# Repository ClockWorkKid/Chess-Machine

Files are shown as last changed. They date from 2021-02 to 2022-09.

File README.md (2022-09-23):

# Chess-Machine
We implemented a chess playing robot that uses an XY plotter machine for manipulating the pieces, webcam for a view of the chessboard and the <a href="https://stockfishchess.org/download/">Stockfish</a> chess engine for calculating moves by the machine. This robot can play chess with a human player.

Demonstration video:
https://youtu.be/TBJXJzK3z6o

[](https://www.youtube.com/watch?v=TBJXJzK3z6o "Click on the image to watch video!")

## Contents
- [Materials Used](#materials-used)
- [Working Procedure](#working-procedure)
- [Hardware Setup](#hardware-setup)
- [Discussion](#discussion)
- [Team](#team)

## Materials Used
Here is a list of materials used for building the chess machine
- PVC board as the base material
- Art papers for coloring the board
- Nylon rods of 1cm diameter as the guide rails
- Linear bearings for sliding alond the rails
- Stepper motors and belts
- A 9g servo motor
- A tiny magnet for holding chess pieces
- IRF540 MOSFETs for stepper motor driver
- A cheap computer PSU
- Arduino UNO for controlling stepper motors
- Lots of wires
- Webcam
- Computer

## Working Procedure
The chess machine has an image based input, a chess engine that works in tandem with MATLAB as the processing unit, and the physical XY plotter that acts as the ouput.

### Detection of Board and Chess Pieces

When a game session starts, the interface prompts the user with a view from the webcam for cropping out the board region. This could be done automatically, but we kept it manual for better precision. The user can crop out the bounding box of the actual board region from the snapshot - this bounding box helps greatly in the detection of chess pieces. The bounding box can be converted to a 8x8 grid that represents the chess board as a table.

We made the board red and blue, and the chess pieces are black and white - this made the overall detection process much easier. The board can be detected using red and blue channels of the RGB image. The white and black chess pieces can be detected using the brightness level. Problem arises when there is overbright or shadowed regions in the chess board that messes with the detection of black and white pieces. For solving this, we trained a regression model for multi-class classification of colors in the board. First, using the "calibrate_samples3.m" funciton multiple samples of red, blue, white and black regions are sampled and then converted to a very small dataset. Then "myOneVsAll.m" funciton is used to trained the logistic regression network for a multi-class classification of color pixels on the chess board. After each pixel is identified as a separate color, we convert the natural board color into a more uniform color distribution where the chess pieces can be more accurately identified. 

In the "get_board3.m" function, an image sample taken by the webcam is first passed through the logistic regression network and then the color channels are used to seperate red, blue, white and black layers.

```
pixels = [ones(size(R)) , R , G , B] ; % unrolled rgb matrix
colors = 1./(1+exp(-(pixels*all_theta'))) > logistic_thres ; % logistic regression prediction
```

White pieces are shown as regions of higher brightness, and black pieces are shown as regions of lower brightness. These are represented as two separate masks, and after morphological opening of these masks and detecting regions, the location of each chess piece can be seen by the computer. 
```
WHITE = imopen(WHITE,strel('disk',noise));
WHITE = ~imopen(~WHITE,strel('disk',noise));
BLACK = imopen(BLACK,strel('disk',noise));
BLACK = ~imopen(~BLACK,strel('disk',noise));

whitePieces = imresize(imcrop(WHITE,stats.BoundingBox),[640 640]);
blackPieces = imresize(imcrop(BLACK,stats.BoundingBox),[640 640]);

%% Identifying objects

detect_white = regionprops(whitePieces,'BoundingBox','Centroid','Area');
detect_black = regionprops(blackPieces,'BoundingBox','Centroid','Area');

```

<figure align="center">
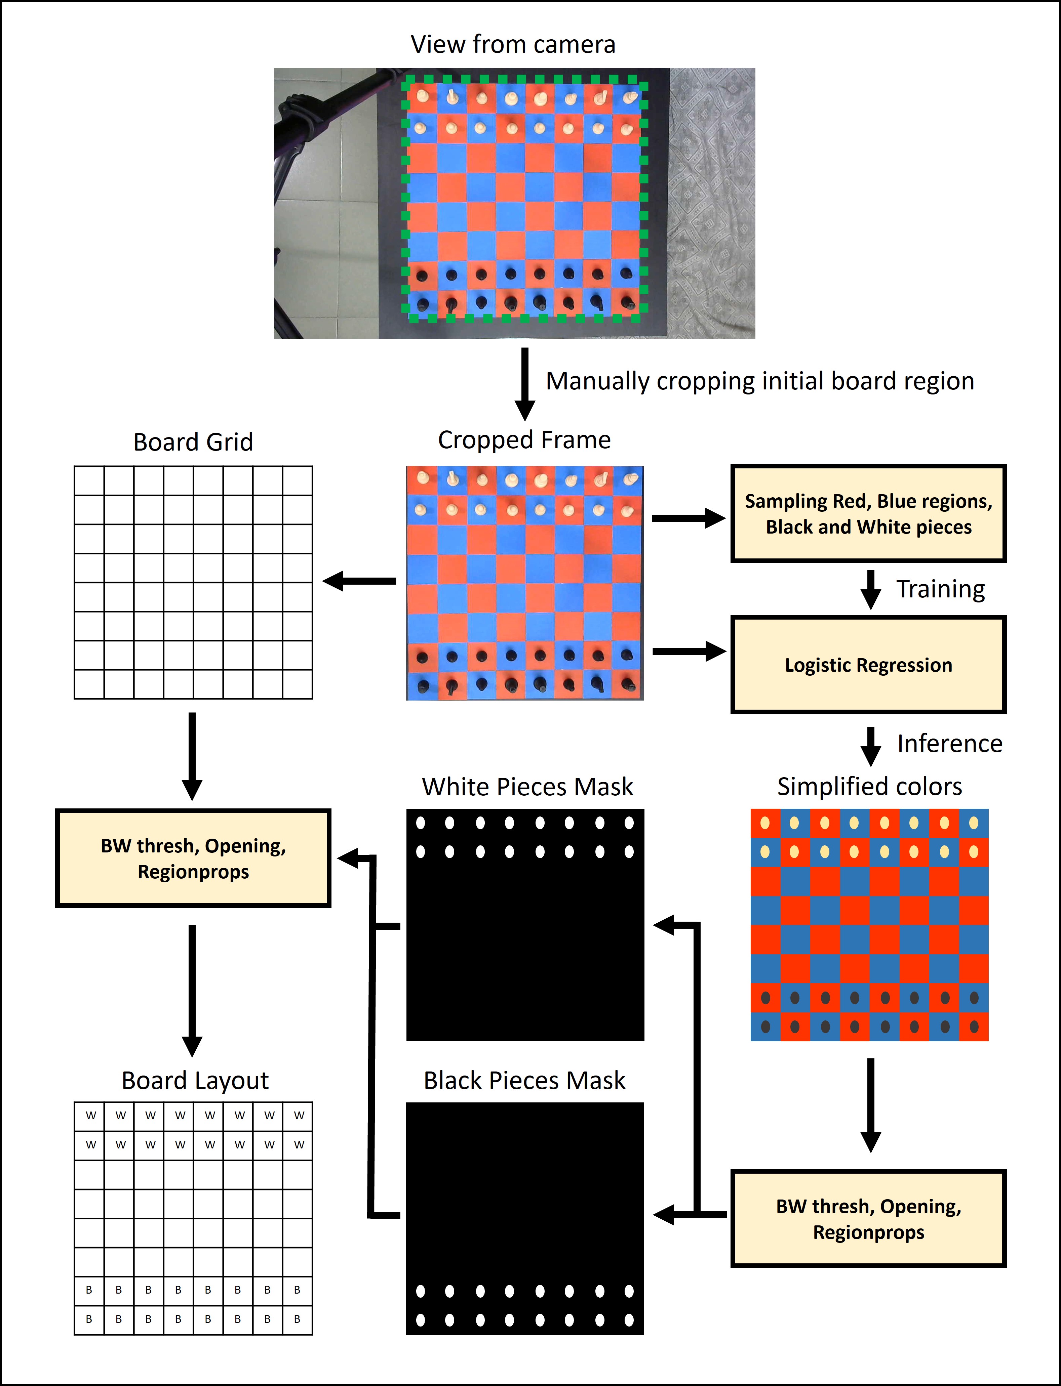
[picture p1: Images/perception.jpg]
    
    <figcaption>Perception framework</figcaption>
</figure>

The region detection function returns the centroids of each of the chess pieces, and we already know the bounding box of the entire board. The board bounding box is converted to a grid of 8x8 and the chess pieces are placed within that grid to know the board positions that are occupied by pieces in a tabular form. Using knowledge of the previous board configuration and comparing it with the current board configuration, we can understand which piece was recently moved. This information is then passed to the custom chess manager that retains memory of the board and checks for validity of moves. 

### Interpreting Board Configuration and Generating Moves

A generic chess game starts from a single position. The perception framework can identify the pieces on the board as black and white pieces only. We detect each piece by observing the displacement between two consecutive snapshots. This helps in determining piece movement, captures etc. The move is then passed to our own implementation of chess logic, that exports the current board configuration into a text format readable by the Stockfish chess engine. 

<figure align="center">
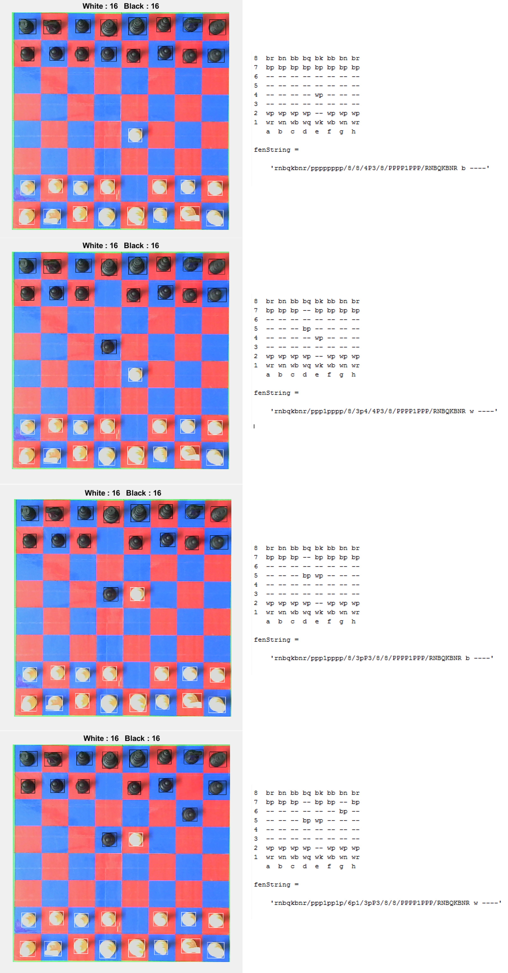
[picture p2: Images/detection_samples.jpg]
    
    <figcaption>Detecting moves and passing to stockfish</figcaption>
</figure>

```
board_new = get_board3(snapshot(cam));
difference_array = xor(board_prev,board_new);

%% implementation of chess logic to detect legality of move
y = checkLegal(b_board, difference_array);

%% update the current board configuration
update(b_board, difference_array)

%% convert to stockfish readable format
fenString = convert_to_fen(b_board)
pass_to_stockfish(fenString)
```

Stockfish can produce the next best move when any board configuration is passed as an input. We then apply a very simple path planning algorithm and send commands to the stepper motors via arduino to move around chess pieces as required by the move.

### Moving the Pieces Around

Say, we want to move a piece from (x1, y1) to (x2, y2). Pieces normally rest at the center of each block. Since the chess machine drags objects magnetically from below the board, direct line movement from block to block would result in conflict between pieces. To solve this, we drag the pieces along the cell borders. When a piece is to be moved, the XY plotter first grabs the piece from the center of a cell, drags it to the corner of the cell, and moves it along the cell edges as shown in the picture. After reaching the destination cell, it places it in the center of the 
target cell. When a piece is to be captured by the machine, the robot would first grab the captured piece, take it outside the chess board, and then replace the target position with the capturing piece. 

<figure align="center">
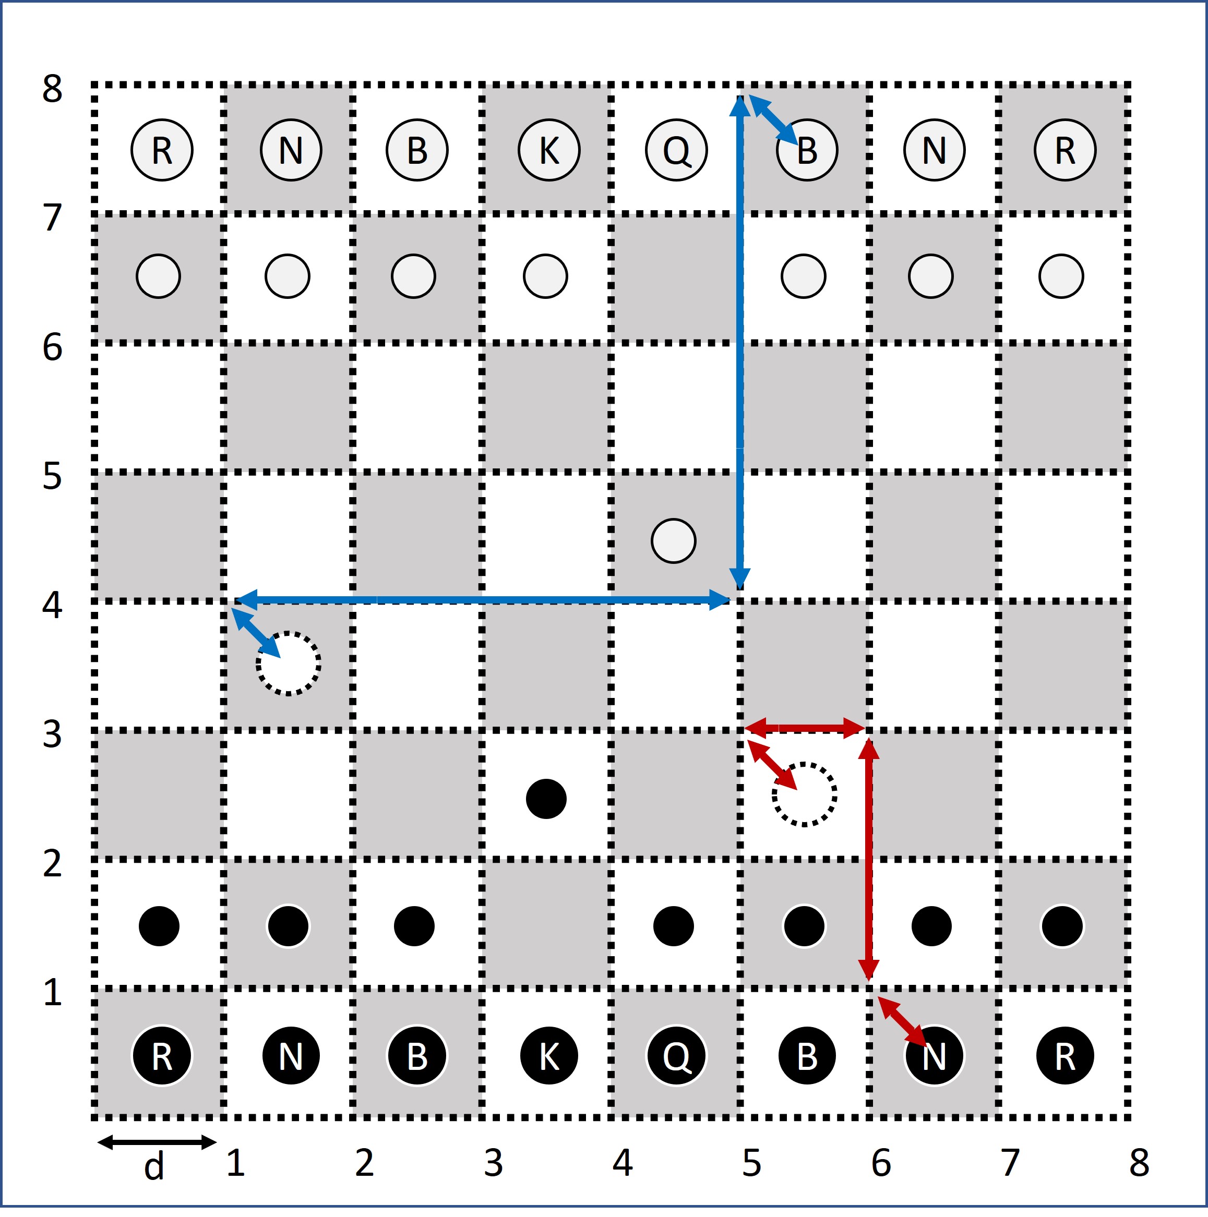
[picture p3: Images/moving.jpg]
    
    <figcaption>Moving around pieces</figcaption>
</figure>

## Hardware Setup

We made initial planning of the hardware using SolidWorks, keeping in mind the use of PVC as the base material for our setup. Some of the dimensions were later changed during implementation. These designs are available in the CAD folder.

<figure align="center">
    
    <figcaption>SolidWorks Design.</figcaption>
</figure>

The axes move on the nylon rails with the help of linear bearings. As pulleys for the stepper motor belts, we had used regular ball bearings. A servo was placed on the second axis, and it had a magnet attached to the tip. A video demonstration of the internals of the XY plotter after the motors were powered: https://youtube.com/shorts/JwAQECdfFwo

[](https://www.youtube.com/watch?v=JwAQECdfFwo "Click on the image to watch video!")

The hardware side of things is connected to Arduino (Arduino Stepper Code > xyplotter3). MATLAB communicates with Arduino via the Serial port and sends commands to it for moving the motors. Arduino moves the axes by switching the poles of the stepper motors. We manually calculated the number of steps required for the requried XY motion. As for the motor driver, we could have used dedicated ICs, but building the motor driver using MOSFETs was quite rewarding. The final circuit is placed inside a little white box to keep things neat. The motors were powered using a cheap computer PSU.

<figure align="center">
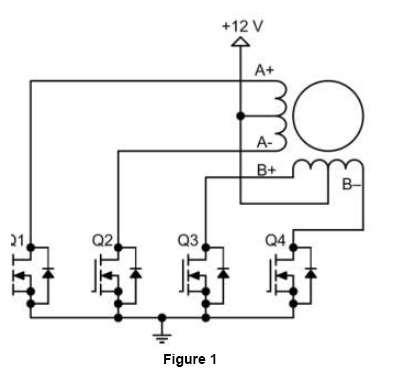
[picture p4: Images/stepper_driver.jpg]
    
    <figcaption>Motor Driver Schematics.</figcaption>
</figure>

## Gallery

<figure align="center">
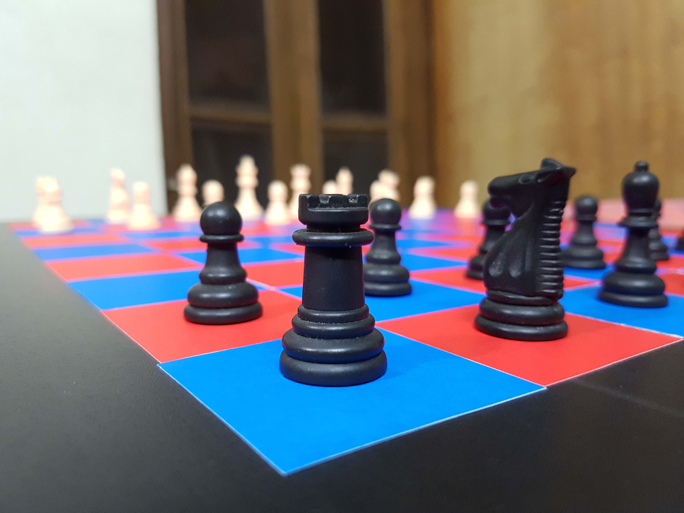
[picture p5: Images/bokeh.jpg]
    
    <figcaption>Starting the build</figcaption>
</figure>

<figure align="center">
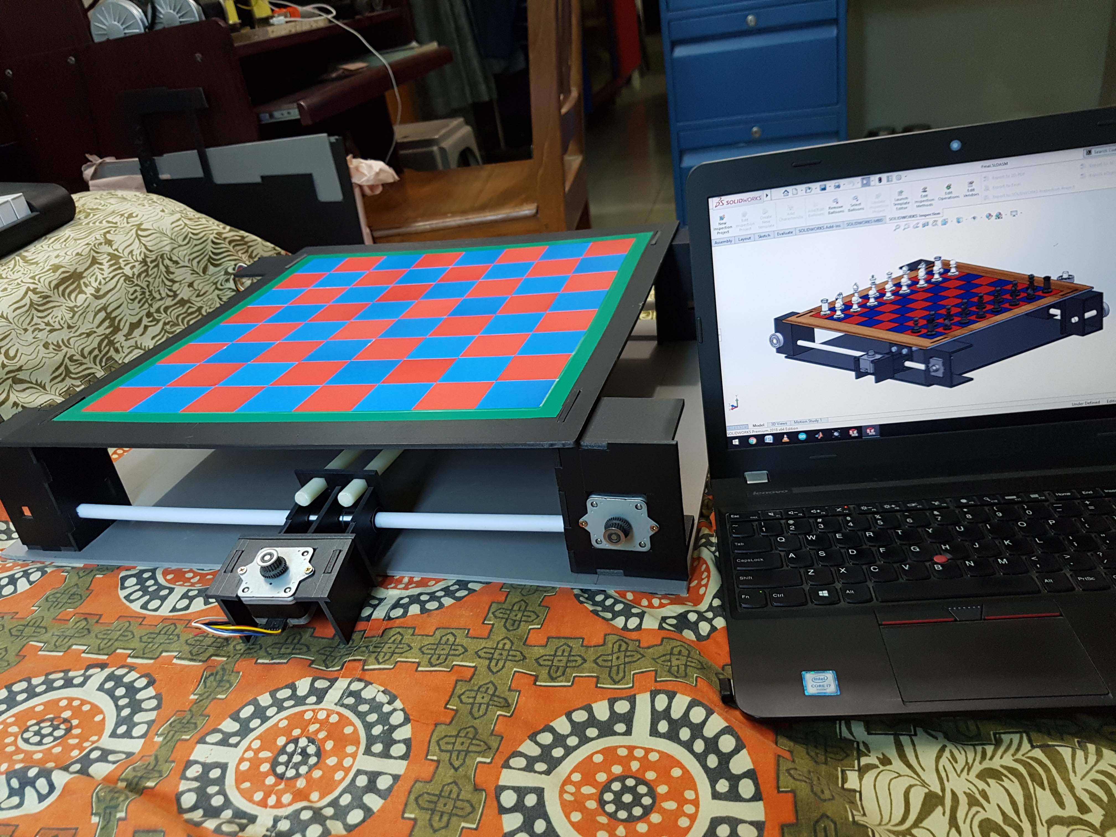
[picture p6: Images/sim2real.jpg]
    
    <figcaption>Bringing to reality</figcaption>
</figure>

<figure align="center">
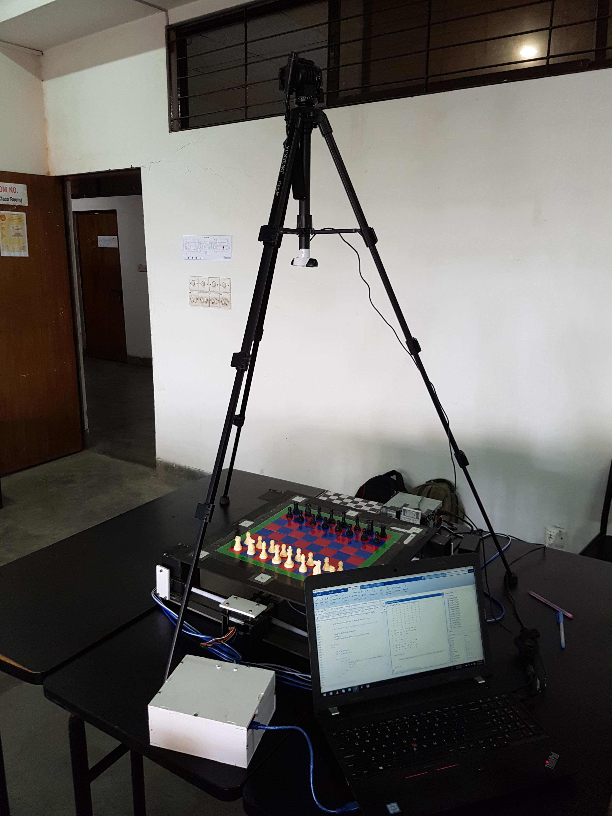
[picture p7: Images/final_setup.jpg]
    
    <figcaption>Setup for project demonstration</figcaption>
</figure>

## Discussion

There are a few shortcomings of the project:
- We have used very cheap materials for the physical hardware. The stepper motors and the belts were especially bad. The board was also malleable, and tended to bend around the center region. The guide-rails were nylon rods, also bendy. No complaints about electrical hardware, just the mechanical part could have been way much better. We stuck to cheap materials because they could be easily modified by hand without needing heavy machinery.
- For the image processing part, we made the board red-blue to easily identify the chess pieces on the board. Normally chess boards are black and white. At that time we didn't have much idea about machine learning or deep learning techniques. Chess pieces on a black and white board can be easily detected using object detection algorithms. Pieces also can be individually identified. Machine learning would also allow the processing to be more robust and environment independent.
- Could have used a dedicated servo motor driver.
- Could have implemented the system using a Raspberry Pi instead of a clunky laptop.

Things that would be cool to implement:
- Training an AI using reinforcement learning to play chess with people
- Remotely playing chess with other human players using the chess machine. (without needing to stare at a computer screen!)

## Team

- Mir Sayeed Mohammad (EEE) (github - https://github.com/ClockWorkKid)
- Shafin Bin Hamid (EEE) (github - https://github.com/shafinbinhamid)
- Himaddri Roy (EEE) (github - https://github.com/himu587)
- Md. Asif Iqbal (EEE)

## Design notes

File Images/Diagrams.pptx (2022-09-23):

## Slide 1

View from camera

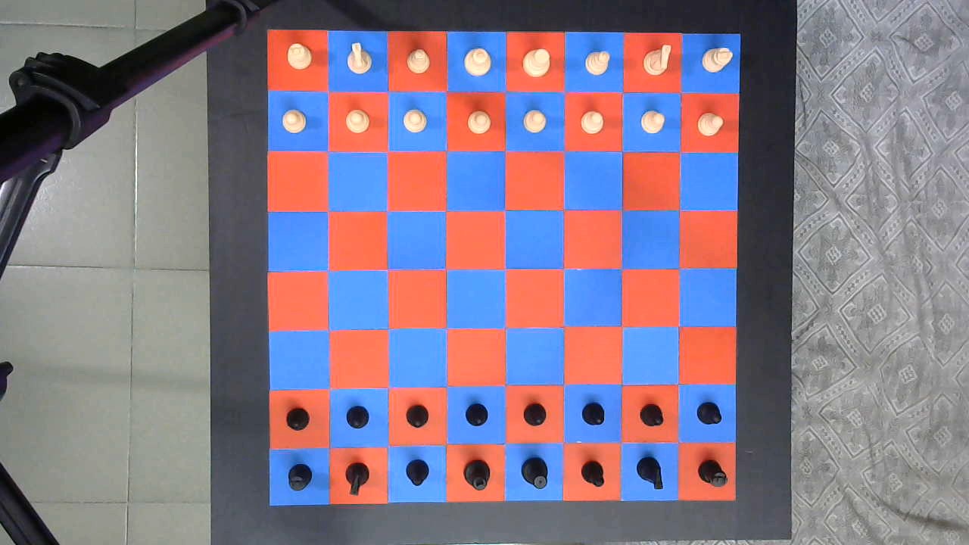
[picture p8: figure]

Manually cropping initial board region

Sampling Red, Blue regions, Black and White pieces

Board Grid

Cropped Frame

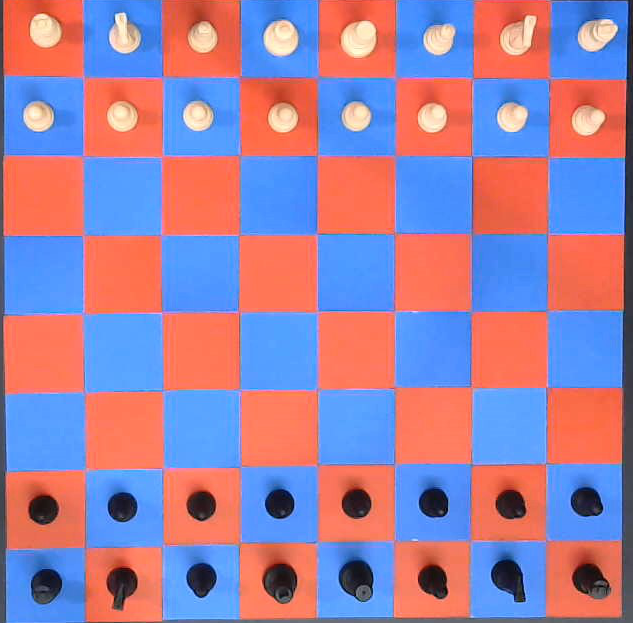
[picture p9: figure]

Logistic Regression

Simplified colors

Training

Inference

BW thresh, Opening, Regionprops

White Pieces Mask

Board Layout

W | W | W | W | W | W | W | W
W | W | W | W | W | W | W | W
B | B | B | B | B | B | B | B
B | B | B | B | B | B | B | B

Black Pieces Mask

BW thresh, Opening, Regionprops

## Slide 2

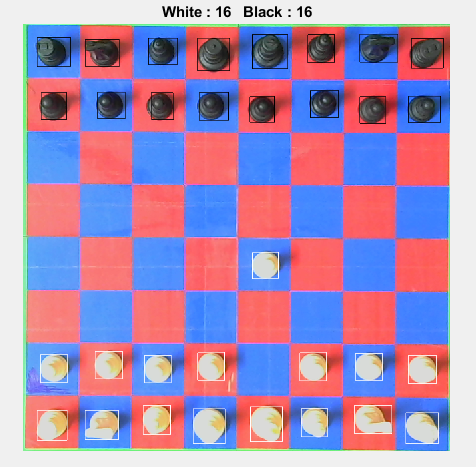
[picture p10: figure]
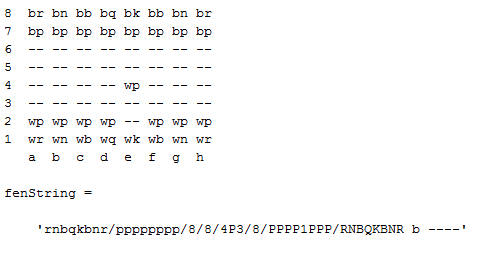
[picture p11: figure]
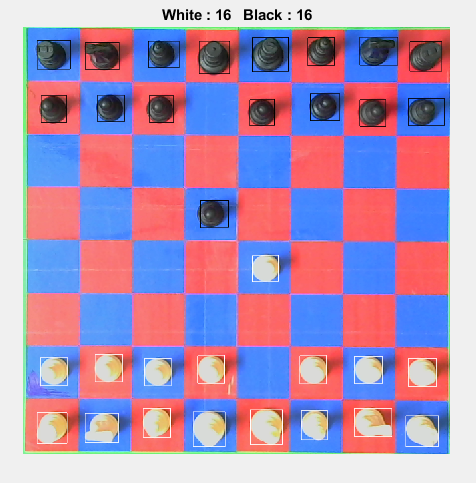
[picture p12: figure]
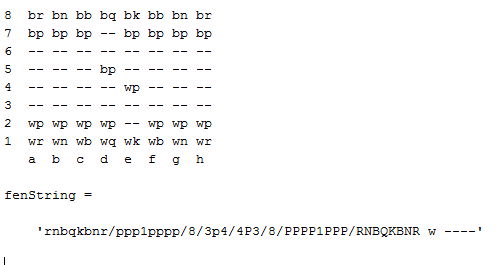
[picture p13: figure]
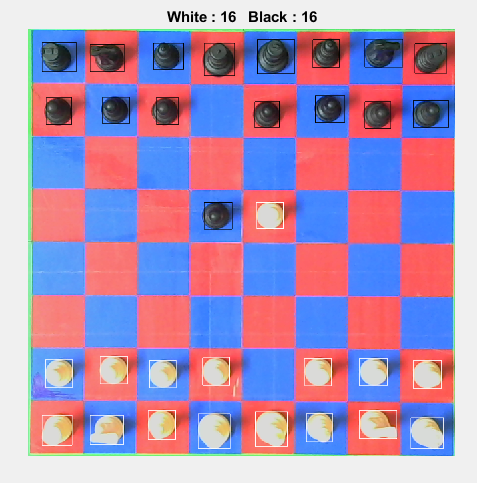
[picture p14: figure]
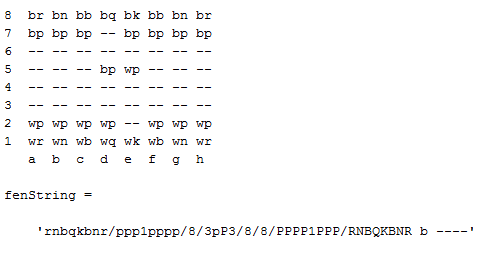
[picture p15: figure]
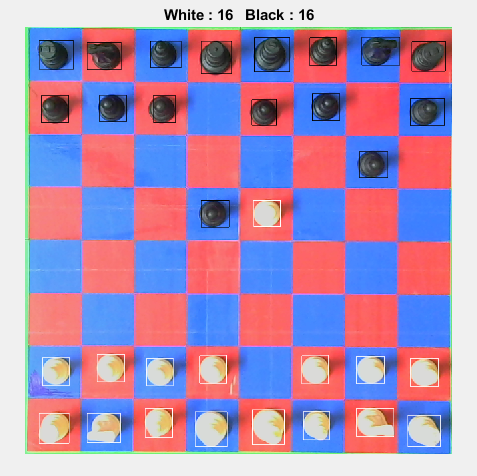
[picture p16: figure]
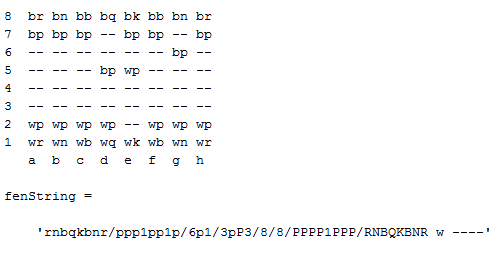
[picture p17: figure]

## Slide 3

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
1 | 2 | 3 | 4 | 5 | 6 | 7 | 8

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
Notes: d

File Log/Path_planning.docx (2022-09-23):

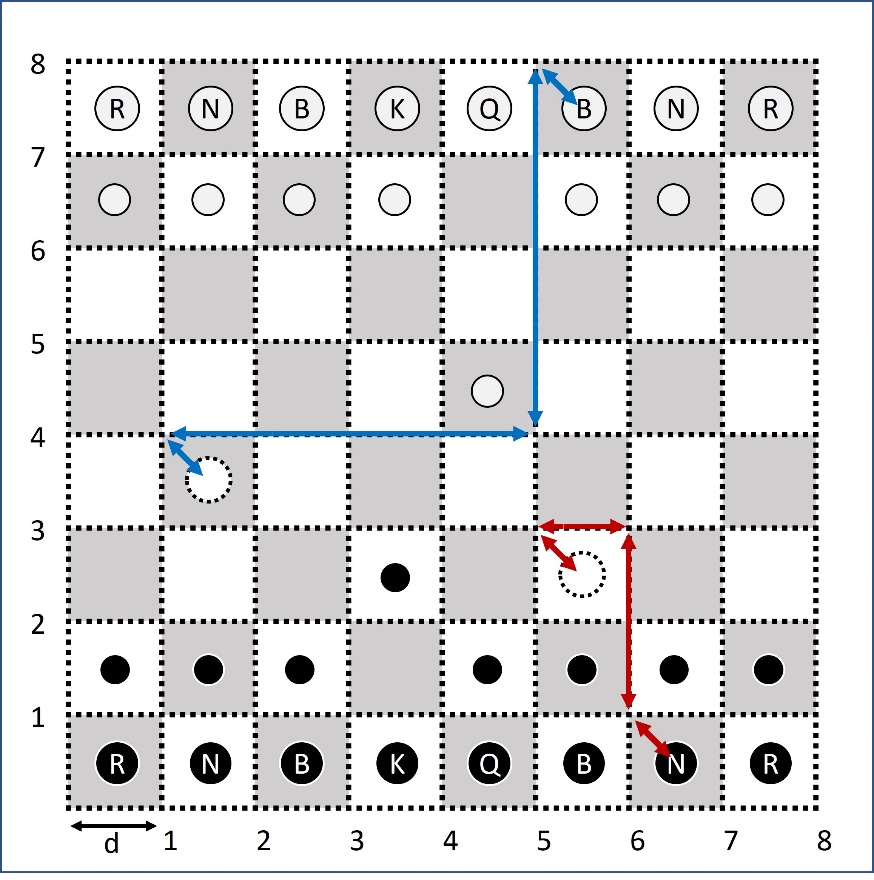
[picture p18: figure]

Say we have to move a piece from (x1, y1) to (x2, y2). The centers are the places where the pieces rest, and the dotted lines are paths to move the pieces. At first, we move the piece from resting place to the path. Then we transfer the piece to desired location and move it back to the resting place. We define a function:

function (x, y) = rest_to_path(x1, y1)

x = x1-d/2;

y =y1+d/2;

end

Main Program:

(x1’, y1’) = rest_to_path(x1, y1);

(x2’, y2’) = rest_to_path(x2, y2);

Move from (x1, y1) to (x1’, y1’);

Move from (x1’, y1’) to (x2’, y2’);

Move from (x1’, y1’) to (x2’, y2’);

Move from (x2’, y2’) to (x2, y2);

The move function is like:

function move(x1, y1, x2, y2)

move along y axis from x1 to x2;

move along x axis from y1 to y2;

end

In this method, the two pieces will never collide because we move them along the path between two pieces. We can add further instructions to the above function like ths:

move(x1, y1, x2, y2)

move servo to (x1, y1)

catch the piece

move along y axis from x1 to x2;

move along x axis from y1 to y2;

release piece

end

current position of the servo is set as a global variable. We can write more functions to do specific tasks:

move_servo(x1, y1)

moves servo from current_position to (x1, y1)

end

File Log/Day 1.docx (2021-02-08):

The Target of our project is to implement a chess engine on a real life interface, meaning you get to play physically against the machine. The chess engine we are using is Stockfish 9. I downloaded the Chess engine, there are the source files for the engine, written in C++ and there are four exe files. The exe files take text commands as inputs and generate results.

So first comes how to use a chess engine. In general a chess engine is a compiled code that can generate results (best move) based upon the current board pieces, and predict future moves by the opponent. The compilation uses a communication protocol, namely the commands that are used to manipulate the engine and get results

When you google on how to use a chess engine, all you get is how to use the engine to improve your game. We are not focused on that. There is the implementation of chess engines using different GUIs

Some of the GUIs are Arena, WinBoard etc.

We are not using GUIs either, so that’s out of the option too

We need data from the engine and use them to instruct our hardware accordingly, meaning that we have to understand the commands and the results generated, acquire the results and process them in our own code

Matlab is being used, so I downloaded a GUI on Matlab, Chessmaster. It is almost the same as other GUIs, but I think we can look into the scripts this GUI uses so that the necessary parts can be extracted from the codes.

Okay, so there are some documents on the chess engine, namely the commands used in UCI communication protocol. Now first you have to open the exe file, it waits for user input.

Input→ position startpos

This starts the board at initial position

Input → position startpos moves d2d4 e7e5….

You can add all the moves played since the beginning to give a view of the current board state to the engine.

Input → position fen r1bqkb1r/pppp1ppp/2n2n2/1B2p3/4P3/2N2N2/PPPP1PPP/R1BQK2R b

This is the board position for any time, you have to learn more about board positions by yourself.

Input → go

Now, this command will predict the next best move for the current player, when you set the position using moves, it will set automatically whose turn it is. But when you use FEN board position, you have to specify in the end whose turn it is, b/w

Output → Bestmove d2d4 ponder e5e7

This is the return value for the command ‘go’. Ponder is the next move predicted by the engine.

How to get fen positions? https://lichess.org/editor/ set up any position you want.

Voice processing

Voice processing is really not an easy task. It requires significant knowledge of machine learning and signal processing, and none of our team has any knowledge in any of those topics. I came across an interesting topic that can help us in understanding the mechanism of machine learning. It says that a perfect speech recognition program works only when you feed it a lot of data, ie train it. This is why google assistant will work far better than anything we can make and train. https://medium.com/@ageitgey/machine-learning-is-fun-80ea3ec3c471

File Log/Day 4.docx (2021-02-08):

Mechanical Design

I have been searching on the web for how to design XY plotter mechanism. Now there are some basic parts that I have been coming across. Some knowledge related to mechanical parts and their names are required to actually find info about that mechanism.

Linear Bearing

These parts are bearings that can slide along any axis. The part widely available in Bangladesh online shops is named scs25uu or sc25uu

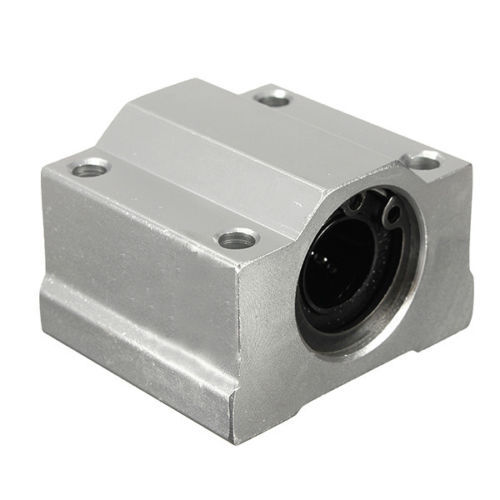
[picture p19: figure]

Linear Guide Shaft

Guide shaft is the part that holds the guide rail in place, and the bearing will slide along the rail.

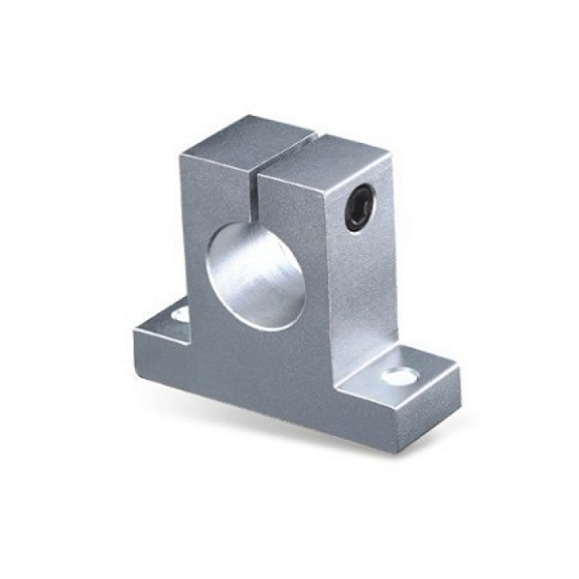
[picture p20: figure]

Guide Rail

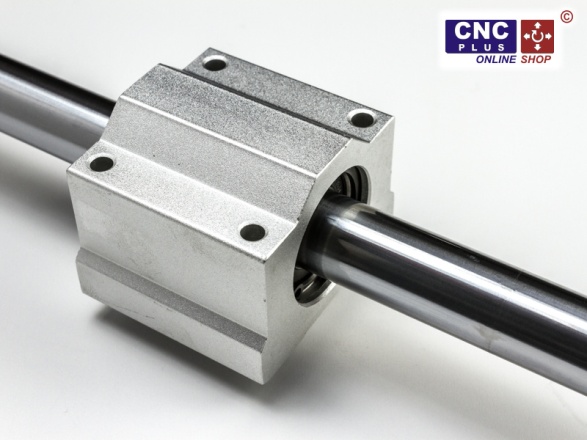
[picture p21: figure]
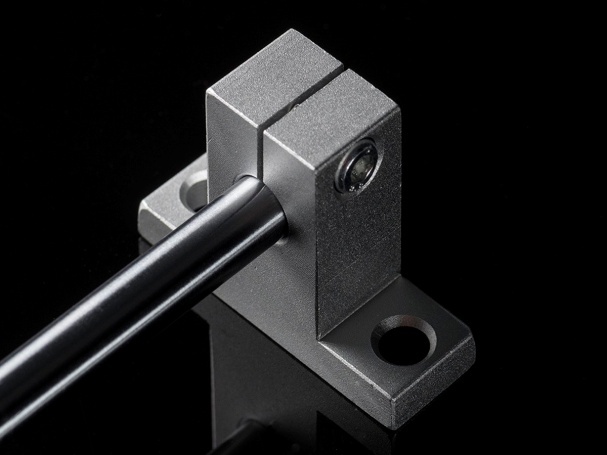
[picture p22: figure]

I have come across a website where you can search for parts and download their 3D designs for implementation on your design

www.traceparts.com

also, there is www.grabcad.com where makers share their own designs and you can download stuff for your use.

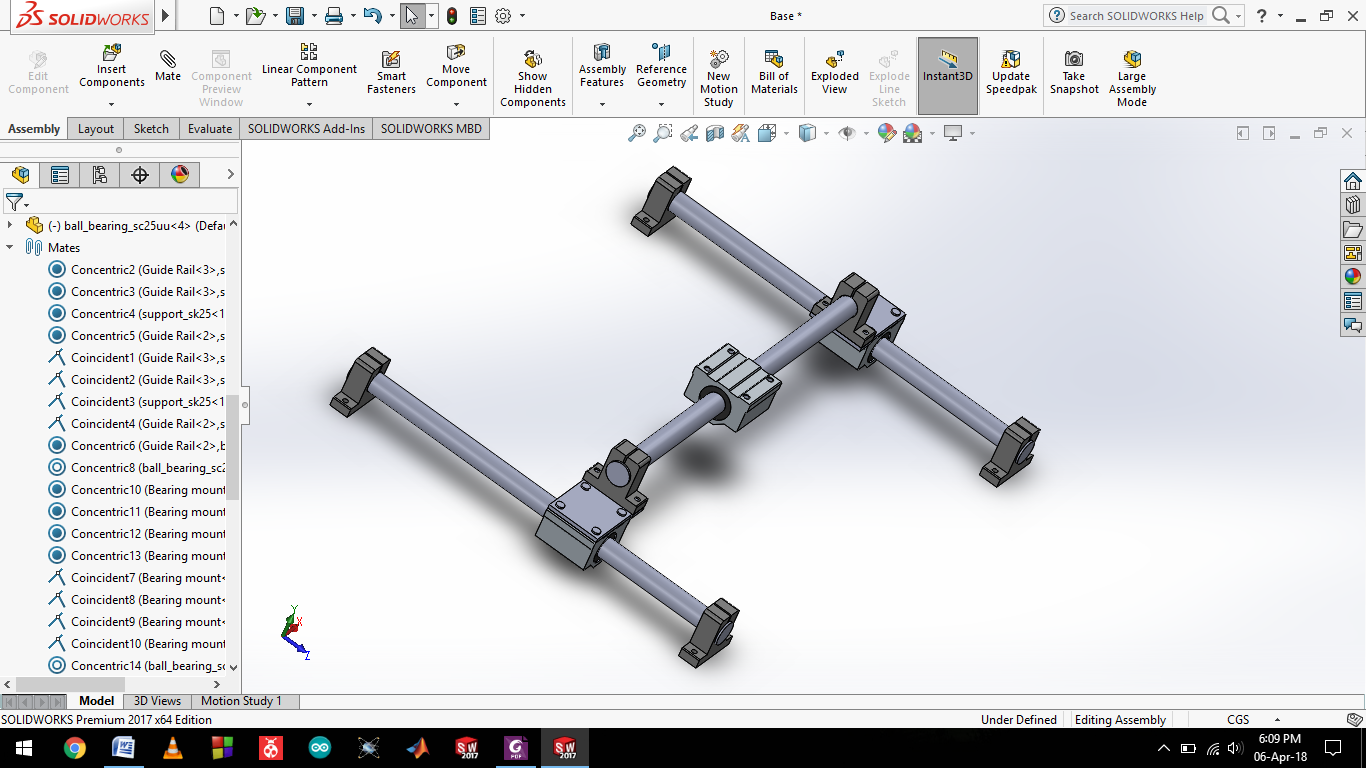
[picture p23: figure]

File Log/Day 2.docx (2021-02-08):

A look into chess notation used here

https://en.wikipedia.org/wiki/Forsyth%E2%80%93Edwards_Notation

Stockfish exe supports command line arguments, obviously.

From windows>R>cmd.exe if you don’t know where the command line is

C:\Users\Sayeed>stockfish.exe

The exe can be used from here just as you used the exe directly.

Input→ quit

This will close the exe file.

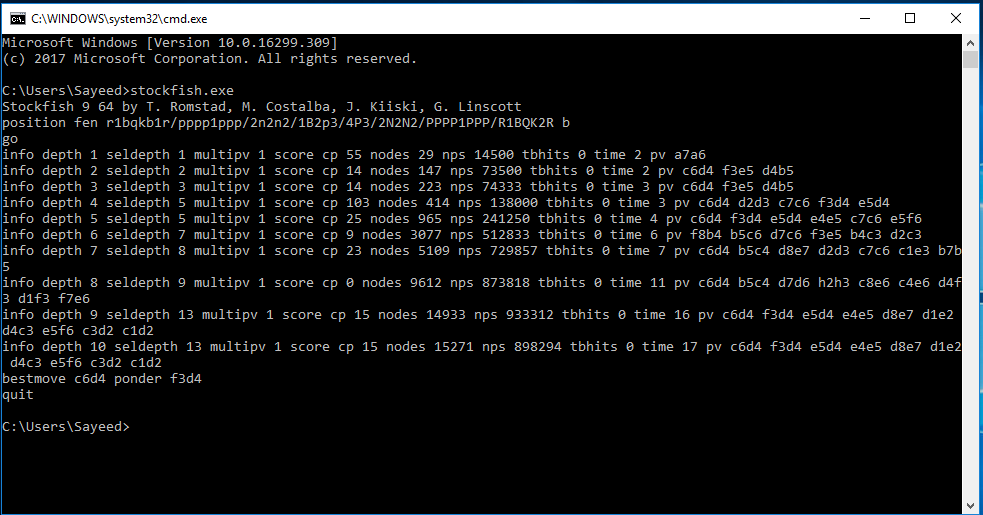
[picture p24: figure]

The command line arguments are also available to the exe, but as far as I have found out, the program quits as soon as you have entered a command, so you cant actually get it to take more commands. So I guess command line wont work this way

I found that Matlab command window can directly use exe files too, the same way as command lines

Input → >> system("D:\stockfish.exe")

And works the same way as the command line.

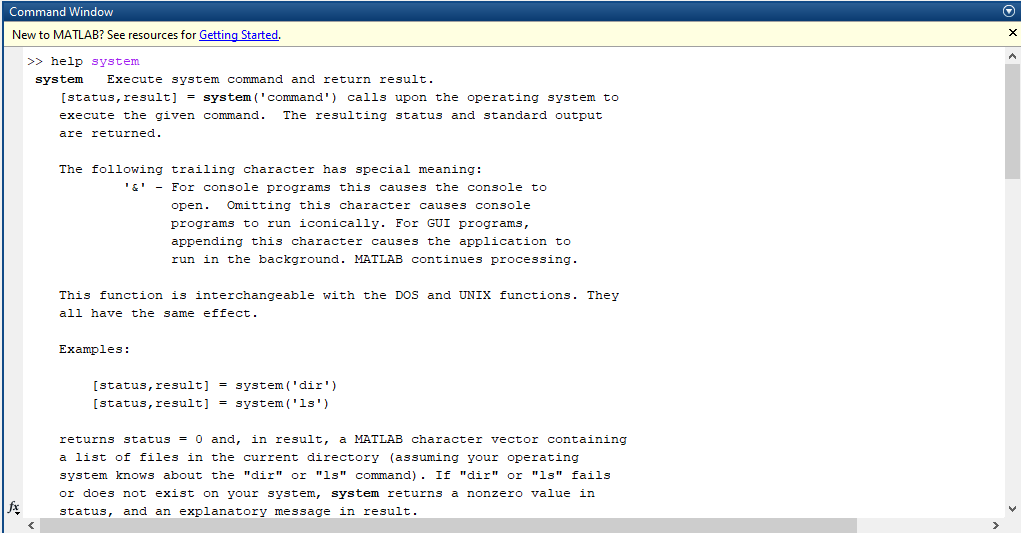
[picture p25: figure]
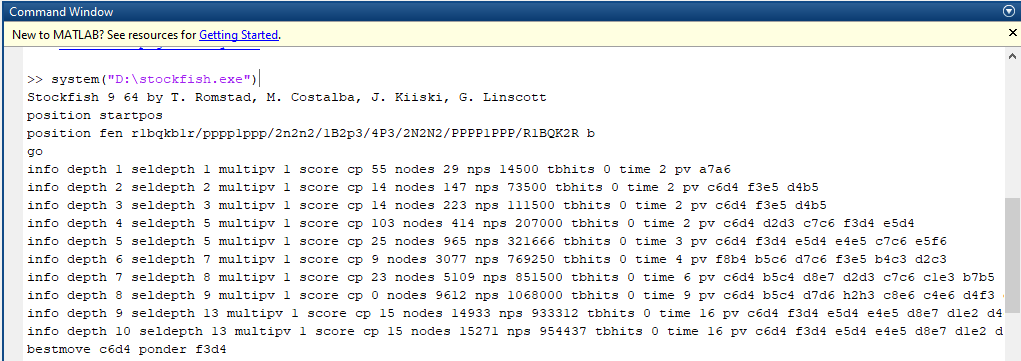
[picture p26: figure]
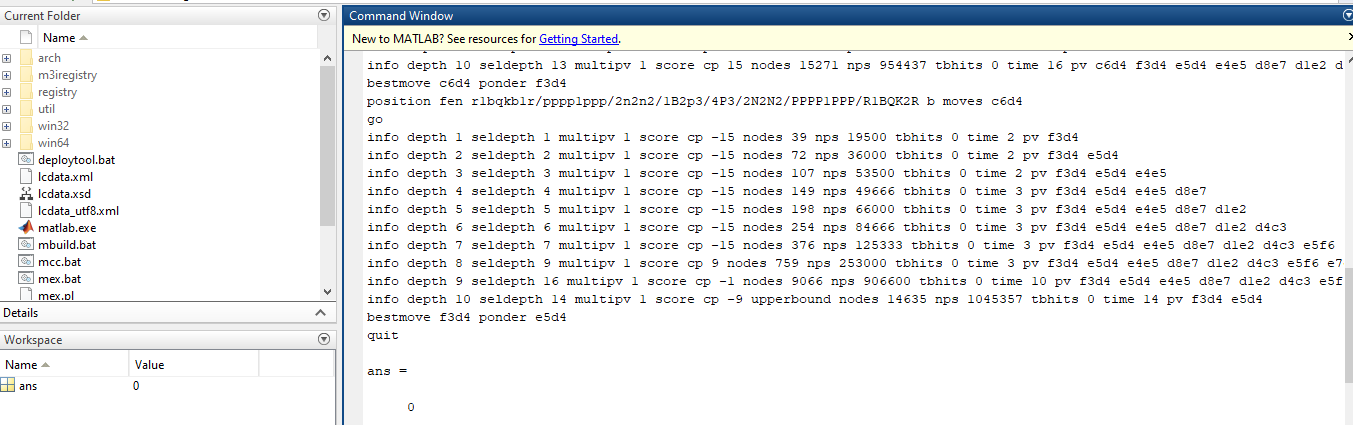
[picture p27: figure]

See how in the last image it returns a zero, meaning that we still haven’t managed to get any return values from the stockfish.exe file. Maybe matlab has some function that can extract and give input to the exe file while working on a script.

Now I have to look into documentation for the system() function. Also I have no clue how matlab processes string data, so documentation for string too.

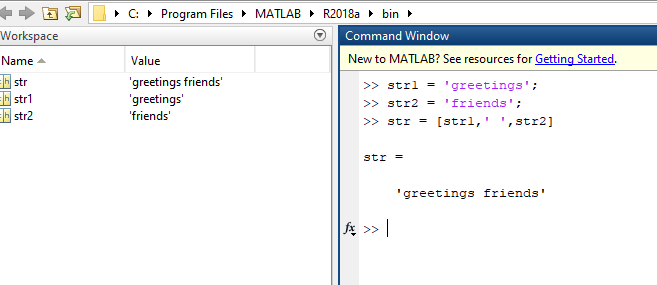
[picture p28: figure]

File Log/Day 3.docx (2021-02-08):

Still looking on how to manipulate an exe file from matlab script. The chessmaster GUI has some functions, and from examining some of the codes, it seems that our required task of passing commands to the engine is done on a file, EngineInterface.m . However I haven’t got a clue how the interfacing is done despite the functions are in front of me.

The required function is SendCommand(), which again uses another structure called uci.gui whatever.

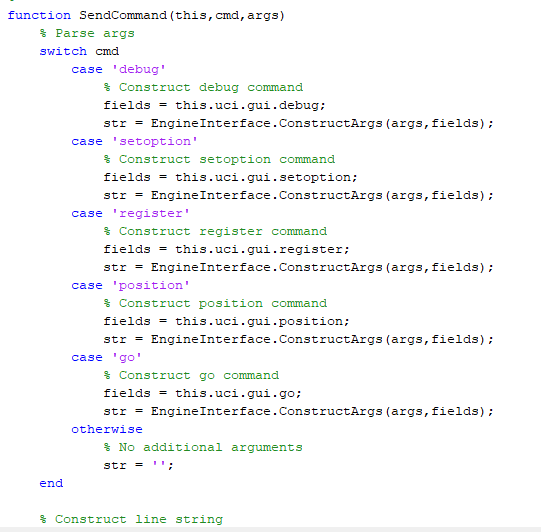
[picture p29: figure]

Machine design

I have some experience on designing robotic parts, in paper of course, and I made a robotic arm for an industrial automation challenge before with PVC sheets. This time I might use pvc too as I don’t have access to machine shop to make parts out of metal etc. And maybe use solidworks for the designing bit so that anyone might reconstruct the whole thing.

Looking into basic mechanisms in CNC machines

http://carbide3d.com/shapeoko/

Didn’t find much useful stuff, I need designs to work on.

Google XY plotter instead

Linear bearing

EngineInterface.m script contains the class definition for the class EngineInterface, this class necessarily handles all the work with the exe file aka the engine.

EngineInterface class has, private and public variables.

Class EngineInterface()

{

Private variables

Const PAUSE_TIME

Const DEF_WAIT_TIME

% Engine search info

info; % Info structure

% Communication variables

p; % Engine process

in; % GUI input (engine output) stream

out; % GUI output (engine input) stream

timerobj; % Asynchronous communication timer

% Internal variables

uci; % UCI commands structure

maxCPU = 1; % Max CPU usage in [0 1]

registerNow = true; % Register now flag

Public variables

name = 'Engine'; % Engine name

author = '??????'; % Engine author

options = {}; % Engine options

% Locks

qlock = false; % Quiet timer-stop lock

rlock = false; % Reading lock

% Engine-associated objects

obj; % ChessEngine/GameAnalyzer parent

EL; % EngineLog object

EO; % EngineOptions object

% Paths

dir;

The underlined three variables are my point of interest as they are doing the main task of communication with the engine.

function [isReady cmd args] = GetCommand(this)

% Get line from engine

[isReady line] = this.GetLine();

GetCommand function has been used in places where we used to expect to see text generated by the engine after hitting enter after commands. We are interested in Getline()

function SendCommand(this,cmd,args)

% Parse args

switch cmd

case 'debug'

% Construct debug command

fields = this.uci.gui.debug;

str = EngineInterface.ConstructArgs(args,fields);

case 'setoption'

% Construct setoption command

fields = this.uci.gui.setoption;

str = EngineInterface.ConstructArgs(args,fields);

case 'register'

% Construct register command

fields = this.uci.gui.register;

str = EngineInterface.ConstructArgs(args,fields);

case 'position'

% Construct position command

fields = this.uci.gui.position;

str = EngineInterface.ConstructArgs(args,fields);

case 'go'

% Construct go command

fields = this.uci.gui.go;

str = EngineInterface.ConstructArgs(args,fields);

otherwise

% No additional arguments

str = '';

end

% Construct line string

line = strtrim(sprintf('%s %s',cmd,str));

% Send line, if non-empty

if ~isempty(line)

% Send line to engine

this.SendLine(line);

end

end

as you can see, the input arguments used for SendCommand are the same ones we used as commands for the stockfish.exe file, so our point of interest is the function SendLine()

function InitializeEngine(this,book)

% Clear info list

this.ClearInfo();

% Tell the engine to use UCI

this.SendCommand('uci');

% Read until 'uciok' is received

this.ReadUntilCMD('uciok');

% Ready handshake

this.ReadyHandshake();

% Make sure debug mode is off

%this.SendCommand('debug',struct('off',true));

% Make sure pondering is off (not supported by ChessEngine)

this.SetOption('Ponder','false');

% Set minimum thinking time to zero

this.SetOption('Minimum Thinking Time','0');

try

% Get # CPU cores

% NOTE: feature() is undocumented

numCores = feature('numCores');

% Set # threads to give desired max CPU usage

% NOTE: Only succeeeds if engine supports "Threads" option

numThreads = sprintf('%.0f',floor(this.maxCPU * numCores));

this.SetOption('Threads',numThreads);

catch %#ok

warnStr = 'Undocumented feature(''numCores'') has failed';

this.EL.AppendWarningLine(warnStr);

end

% Set up opening book access

if ~isempty(book)

% Tell the engine to use its own book

% NOTE: Only succeeds if engine supports "OwnBook" option

this.SetOption('OwnBook','true');

% Give the engine the specified opening book path

% NOTE: Only succeeds if engine supports "Book File" option

this.SetOption('Book File',this.AbsPath(book));

else

% Tell the engine *not* to use its own book

% NOTE: Only succeeds if engine supports "OwnBook" option

this.SetOption('OwnBook','false');

end

% Tell the engine to start a new game internally

this.SendCommand('ucinewgame');

end

This function InitializeEngine() is used to optimize the engine for gameplay, there are some functions here that we have not discussed, so we will be replacing them with our own functions, namely by sending the specified commands and processing the responses ourselves, with less funcitions.

function [isReady line] = GetLine(this)

% Read line from input stream

isReady = this.in.ready();

if (isReady == true)

% Get line from input buffer

line = char(this.in.readLine());

% Write nonempty lines to engine log

if ~isempty(line)

this.EL.AppendEngineLine(line);

end

else

% Engine had nothing to send

line = '';

end

end

function SendLine(this,line)

% Send line to output stream

this.out.println(line);

%this.out.flush();

% Write line to engine log

this.EL.AppendGUILine(line);

end

we have found the two functions we have been looking for, now the problem is that we still don’t know what in.ready(),in.readLine(),out.println(line); functions are doing here. So we have to find the in & out variables.

Luckily, the function immediately after these explains a lot for us

function OpenLink(this,path)

% Make sure we have the absolute path

path = this.AbsPath(path);

% (Try to?) set execute permissions

if (ispc == true)

% Windows

usr = 'Everyone';

cmd = sprintf('icacls "%s" /grant %s:RX',path,usr);

[~,~] = system(cmd);

else

% Mac

usr = 'ugo';

cmd = sprintf('chmod %s+x "%s"',usr,path);

[~,~] = system(cmd);

end

% Spawn engine process

%this.p = java.lang.Runtime.getRuntime().exec(path);

this.p = java.lang.ProcessBuilder(path).start();

% Connect to engine's stdout

iStream = this.p.getInputStream();

iStreamReader = java.io.InputStreamReader(iStream);

this.in = java.io.BufferedReader(iStreamReader);

% Connect to engine's stdin

oStream = this.p.getOutputStream();

this.out = java.io.PrintWriter(oStream,true);

%this.out = java.io.PrintWriter(oStream);

end

The underlined three lines are the definitions of the variables that we had discussed earlier, our point of interest. Now lets take a look into them.

p, in and out are basically three objects, namely java objects. P is a process object, java.lang.ProcessBuilder(path) is a processbuilder object, that works on a file specified by ‘path’, and path will be the path to our stockfish.exe. Now java.lang.ProcessBuilder(path).start() will start a process, and we get our p process object.

The process has to get an input stream, input stream of java(matlab) receives the stream of data that the engine(process) is generating(outputting) for us, which is done in the % Connect to engine's stdout section. Note that by this, we are getting output data generated by the engine.

Output stream of java(matlab) sends the stream of data that the code is generating(outputting) by us, and engine(process) takes as input, which is done in the % Connect to engine's stdin section. Note that by this, we are sending output data generated by our code.

Okay, so, that brings us to the final code that I have created by changing some stuff

clear all; %just my habit

clc;

%import all the java class files

import java.lang.ProcessBuilder;

import java.io.InputStreamReader;

import java.io.PrintWriter;

import java.io.BufferedReader;

command = 'position startpos'; %dummy command

path = "D:\stockfish.exe"; %setting the path to our engine

%process started

processBuilderObject = ProcessBuilder(path);

process = processBuilderObject.start();

%output stream connected(the commands that we will send)

oStream = process.getOutputStream();

out = PrintWriter(oStream,true);

%input stream connected(the results that engine generates)

iStream = process.getInputStream();

iStreamReader = InputStreamReader(iStream);

in = BufferedReader(iStreamReader);

%functions we will use to send and receive data

%in.ready();

%in.readLine();

%out.println(command);

I have written these in a script, and then executing the script brings us to the step from where we can use the command window to either communicate with the engine, as well as do whatever other processes we wish to execute.

For example, ive run the script once, and then run the following from the command window:

>> in.ready()

ans =

logical

1

>> in.readLine()

ans =

Stockfish 9 64 by T. Romstad, M. Costalba, J. Kiiski, G. Linscott

>> out.println('position fen rnbqkb1r/p2ppppp/5n2/1ppP4/2P5/8/PP2PPPP/RNBQKBNR w KQkq -');

>> out.println('go');

>> in.ready()

ans =

logical

1

>> in.readLine()

ans =

info depth 1 seldepth 1 multipv 1 score cp 150 nodes 57 nps 19000 tbhits 0 time 3 pv c4b5 d8a5 b1c3

>> in.readLine()

ans =

info depth 2 seldepth 3 multipv 1 score cp 150 nodes 111 nps 37000 tbhits 0 time 3 pv c4b5 d8a5 b1c3

>> in.readLine()

ans =

info depth 3 seldepth 4 multipv 1 score cp 80 nodes 206 nps 68666 tbhits 0 time 3 pv c4b5 d8a5 b1c3 d7d6

>> in.readLine()

ans =

info depth 4 seldepth 5 multipv 1 score cp 120 nodes 281 nps 93666 tbhits 0 time 3 pv c4b5 d8a5 b1c3 d7d6 e2e3

>> in.readLine()

ans =

info depth 5 seldepth 6 multipv 1 score cp 73 nodes 805 nps 268333 tbhits 0 time 3 pv c4b5 d7d6 b1c3 b8d7 c1d2

>> in.readLine()

ans =

info depth 6 seldepth 6 multipv 1 score cp 112 nodes 1379 nps 344750 tbhits 0 time 4 pv c4b5 d7d6 b1c3 c8f5 e2e4 f6e4

>> in.readLine()

ans =

info depth 7 seldepth 8 multipv 1 score cp 102 nodes 2270 nps 454000 tbhits 0 time 5 pv c4b5 e7e6 b1c3 e6d5 c3d5 d7d6 d5c3

>> in.readLine()

ans =

info depth 8 seldepth 9 multipv 1 score cp 118 nodes 4797 nps 599625 tbhits 0 time 8 pv c4b5 a7a6 e2e4 f6e4 d1e2 e4d6 b1c3 a6b5 c3b5 d6b5

>> in.readLine()

ans =

info depth 9 seldepth 12 multipv 1 score cp 82 nodes 12900 nps 921428 tbhits 0 time 14 pv c4b5 a7a6 e2e3 a6b5 f1b5 d8a5 b1c3 e7e6 d5e6 f7e6

>> in.readLine()

ans =

bestmove c4b5 ponder a7a6

So, in.ready() is to check if there is any output by the engine that we haven’t received yet, don’t use in.readLine() without checking first, otherwise if there is no engine output, the process keeps standing there for eternity. Out.println(command) sends the command as necessary.

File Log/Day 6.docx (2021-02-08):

There are two toolkits that got my attention, one is HTK toolkit, and the other is CMU Sphinx.

Now, I started looking in the tutorial of HTK, and the whole thing is huge. So it might require a lot of time. In the meantime, Googled Python speech recognition module, got me to the site

https://pypi.python.org/pypi/SpeechRecognition/

so from there, downloaded the speechrecognition toolkit, a file named

SpeechRecognition-3.8.1-py2.py3-none-any.whl

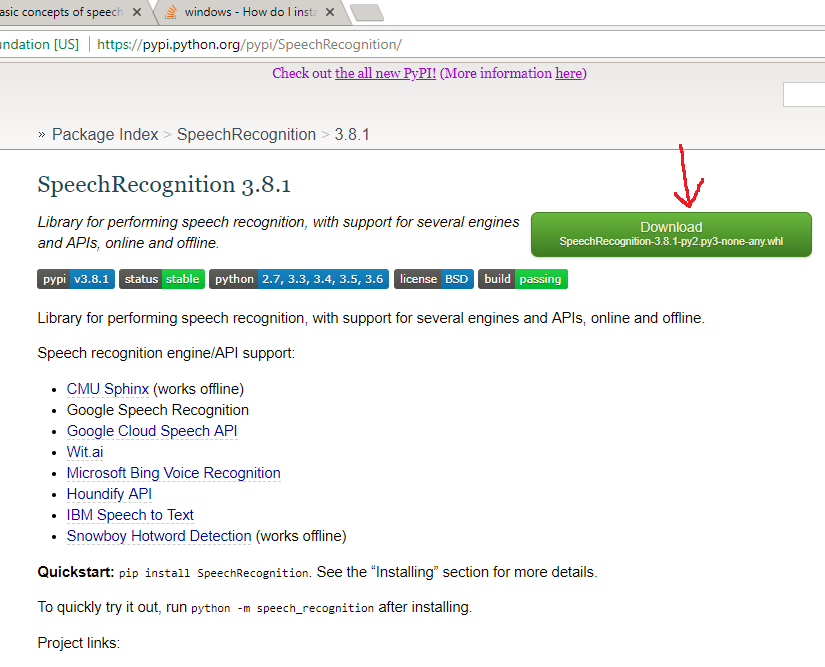
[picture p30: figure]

After downloading, went to the windows command line, activated my anaconda workshop environment, and installed the module.

- activate workshop
- pip install D:/ SpeechRecognition-3.8.1-py2.py3-none-any.whl
- pip install PyAudio

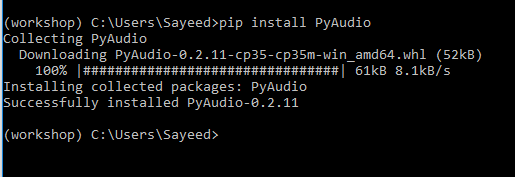
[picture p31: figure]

Download the file

https://github.com/Uberi/speech_recognition/blob/master/third-party/pocketsphinx-0.1.3-cp35-cp35m-win_amd64.whl

https://github.com/Uberi/speech_recognition/blob/master/examples/microphone_recognition.py

ran this example while commenting out the other engines and APIs except cmusphinx


Running the module, you have to wait for a while when the program is looking for speech, and then it generates results.

I actually said, ‘Hello speech recognition say something’

But this is something to work on, so I think we have a stepping stone in our progression now.

CMUSphinx has a full documentation and tutorial, although we are using PocketSphinx, I think the tutorials are worth looking into.

https://cmusphinx.github.io/wiki/

Maybe we should look into the dictionary used by sphinx, and make oun dictionary with necessary training data.

Interfacting with matlab

The system() function in matlab can directly execute system command and return result. So we can use this to call the python interpreter during runtime of any matlab script.

Example:

- system(‘python somecode.py’);

This works almost the same as running python from windows command line.

But in the previous steps we have set up the entire speech recognition module inside the environment ‘workshop’. So somehow either we have to set up the environment inside matlab and run our voice processing code inside that environment, or we have to set up the speech recognition module inside the base environment of python.

For some reason, I could not install the pocketsphinx library inside the base environment.

And when used in two different lines, the environment setup doesn’t hold, for example:


So we just have to pipe the two commands so that the python script can work inside the environment.


Clarifying, again, it isn’t working, I said “Hello testing one two three four five” and this is what it thinks.

So adjusting the speech recognition part is later, and to make things work, meaning that for using whatever text that the toolkit is showing us, we somehow have to read those lines from the matlab command window and feed it into our script for further processing. The specific code that ran in the previous line is as follows:

D:\test.py

import speech_recognition as sr

# obtain audio from the microphone

r = sr.Recognizer()

with sr.Microphone() as source:

print("Say something!")

audio = r.listen(source)

# recognize speech using Sphinx

try:

print("Sphinx thinks you said ")

print(r.recognize_sphinx(audio))

except sr.UnknownValueError:

print("Sphinx could not understand audio")

except sr.RequestError as e:

print("Sphinx error; {0}".format(e))

Found a function that can nest commands inside it and after execution of that command, saves whaever output is shown in the command window as a string, which can be used later for other processes.


See how the supposed output of the command x = sin(0:.5:2*pi) was not shown in execution, but the whole thing has been saved as a string inside a. We can use this process to convert whatever output the python program shows in the command window and extract our required voice data from that string.

clear all;

close all;

clc;

a=evalc('system(''activate workshop && python D:\test.py'')');

a=compose(a);

a=char(a);

C = strsplit(a,'\n');

disp(C(1));

now C(1) contains voice processed string output.

Google speech API

pip install google-api-python-client

Add the following part to our previous test.py code to add google voice recognition api.

# recognize speech using Google Speech Recognition

try:

# for testing purposes, we're just using the default API key

# to use another API key, use `r.recognize_google(audio, key="GOOGLE_SPEECH_RECOGNITION_API_KEY")`

# instead of `r.recognize_google(audio)`

print("Google Speech Recognition thinks you said " + r.recognize_google(audio))

except sr.UnknownValueError:

print("Google Speech Recognition could not understand audio")

except sr.RequestError as e:

print("Could not request results from Google Speech Recognition service; {0}".format(e))


I said “Hello Testing 1 2 3 4 5 D2 D4”

For some reason Hello Testing went missing

But Google Speech API works far better than pocketsphinx

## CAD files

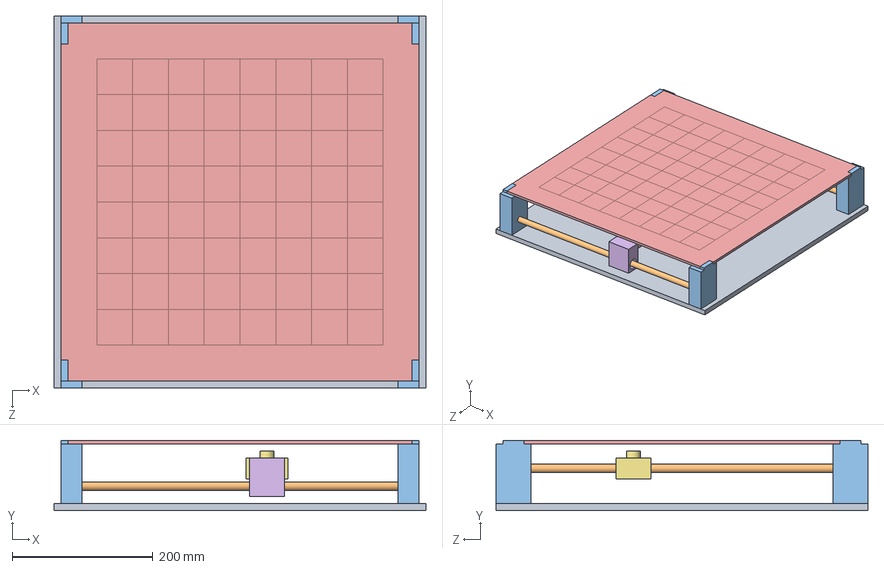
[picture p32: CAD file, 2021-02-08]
CAD/Build 1/Base1.SLDASM
528.0 x 100.0 x 528.0 mm
groundPlate
rail12mm x 4
RailMount x 4
LM12UU x 4
Board
RailMount2 x 2
MagnetMount

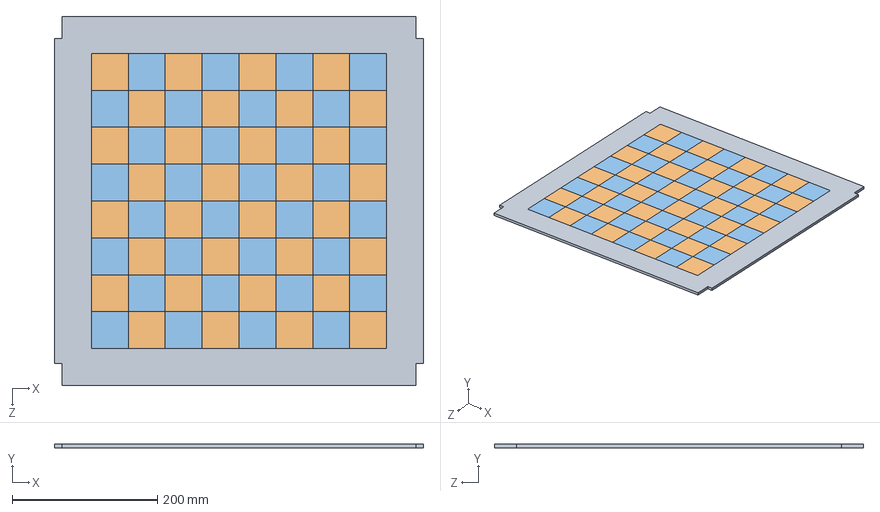
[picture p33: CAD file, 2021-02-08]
CAD/Build 1/Board.SLDASM
508.0 x 5.00 x 508.0 mm
board_base
board_dark x 32
board_white x 32

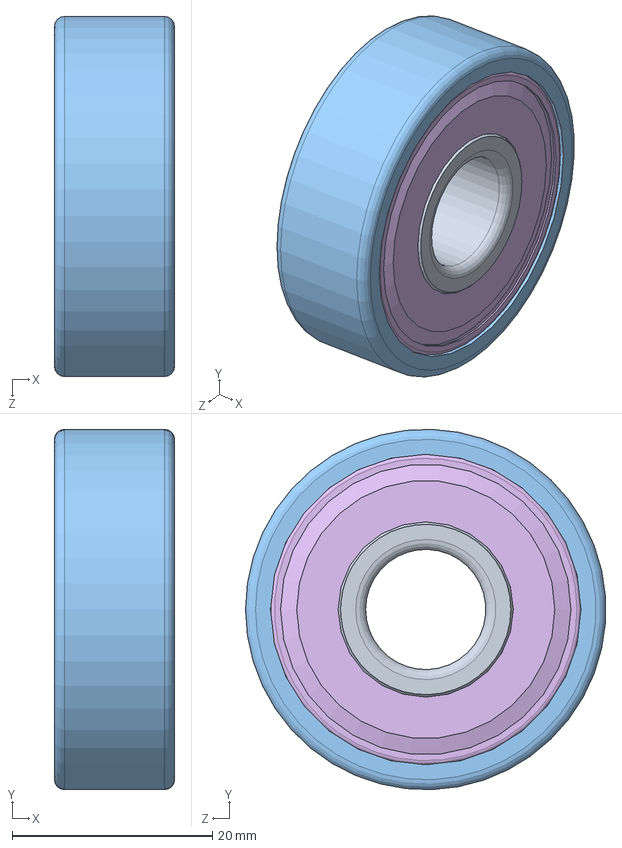
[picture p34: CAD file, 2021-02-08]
CAD/Build 1/Bearing/Bearing.SLDASM
12.0 x 36.0 x 36.0 mm
Inner Race
Ball x 6
Outer Race
Cage x 2
Pin x 6
Shield x 2

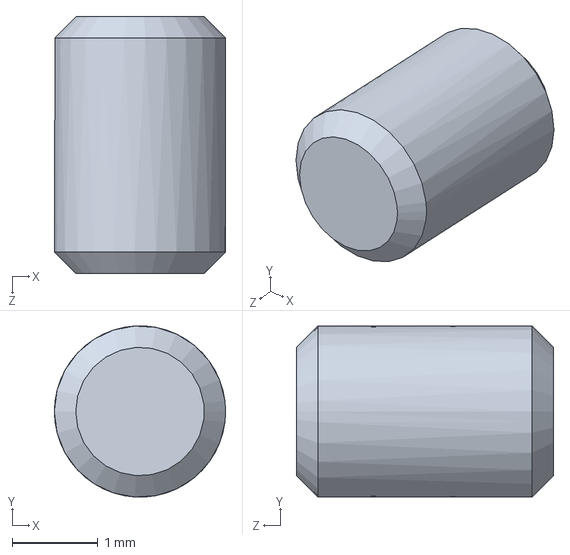
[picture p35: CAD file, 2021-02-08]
CAD/Build 1/Bearing/Pin.SLDPRT
2.00 x 2.00 x 3.00 mm

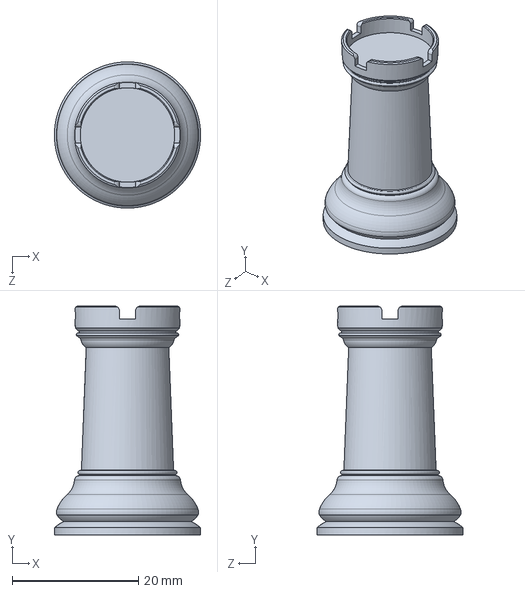
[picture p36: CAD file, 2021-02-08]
CAD/Build 1/ChessPieces/Rook.SLDPRT
23.2 x 36.3 x 23.2 mm

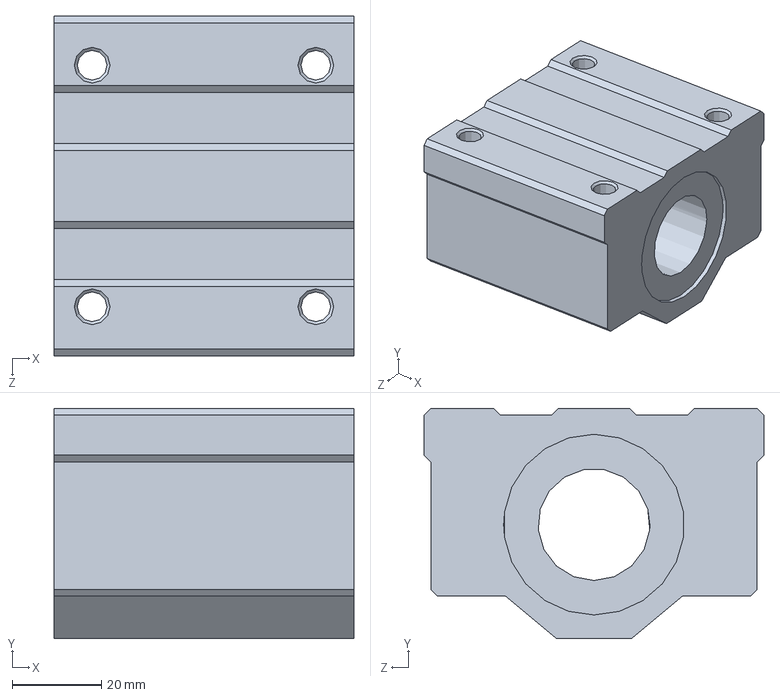
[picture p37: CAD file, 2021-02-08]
CAD/Build 1/Traceparts/ball_bearing_sc25uu.SLDPRT
67.0 x 51.5 x 76.0 mm

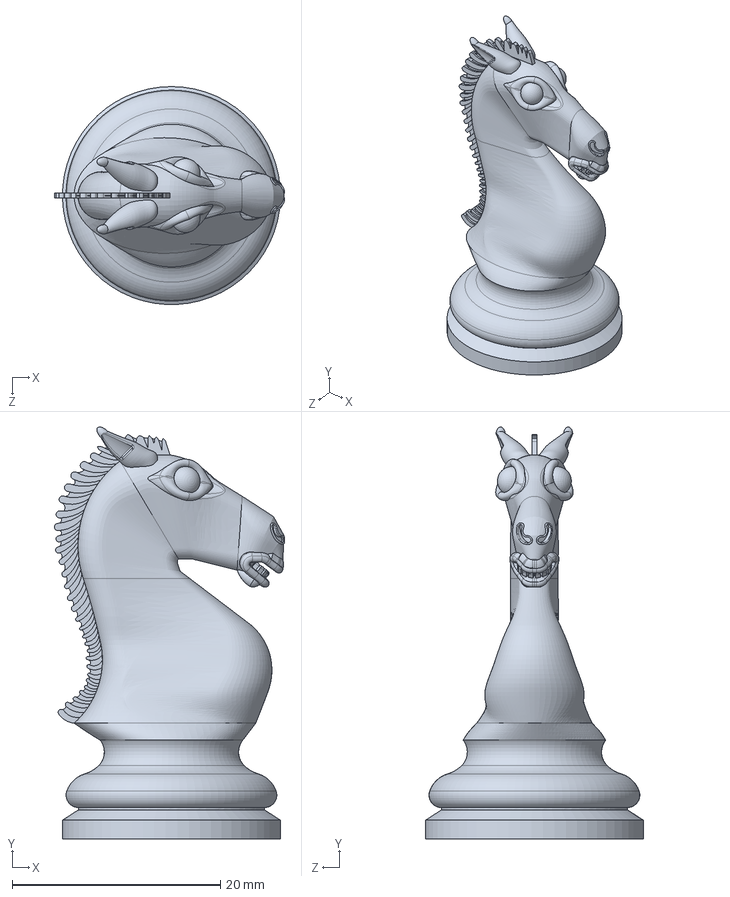
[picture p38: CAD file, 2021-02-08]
CAD/Build 2/Pieces/P_White_Knight.SLDPRT
22.1 x 39.6 x 20.9 mm

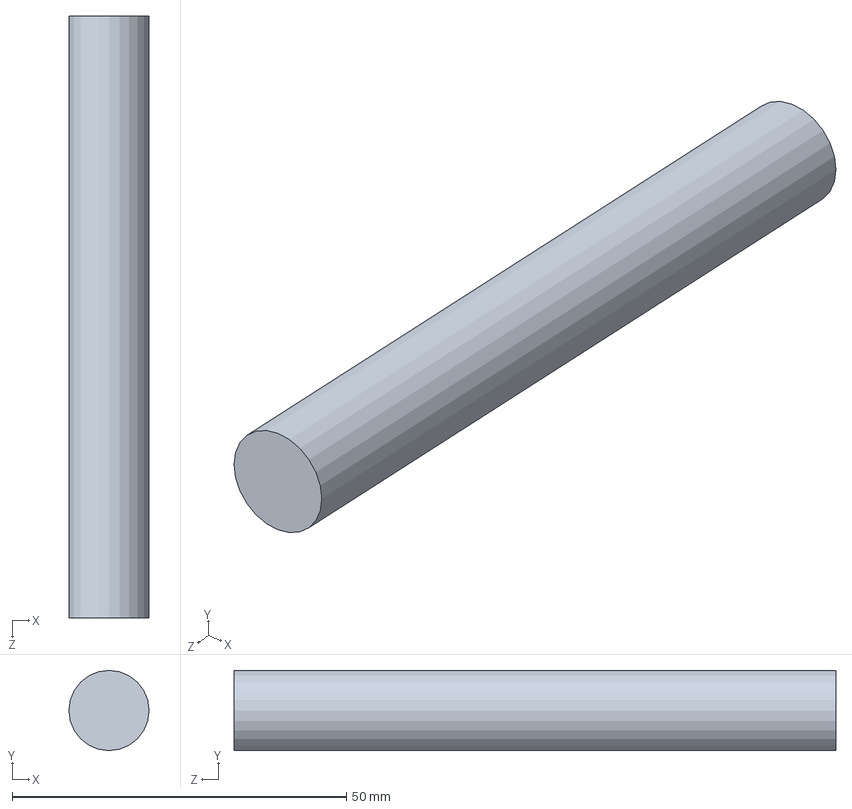
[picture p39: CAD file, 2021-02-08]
CAD/Build 2/rail12mmBearing.SLDPRT
12.0 x 12.0 x 90.0 mm

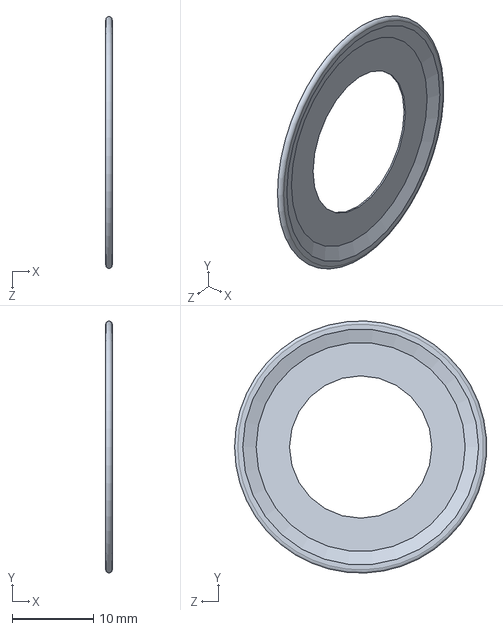
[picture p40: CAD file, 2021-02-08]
CAD/Build 1/Bearing/Shield.sldprt
0.8 x 31.0 x 31.0 mm

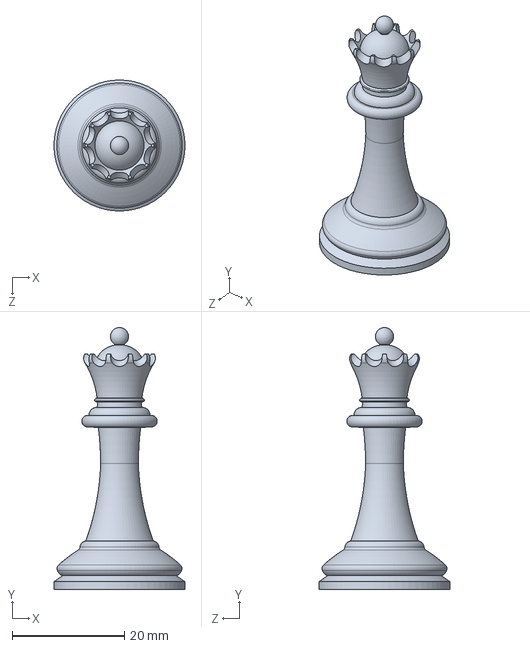
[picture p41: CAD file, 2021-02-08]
CAD/Build 1/ChessPieces/Queen.SLDPRT
23.3 x 46.7 x 23.3 mm

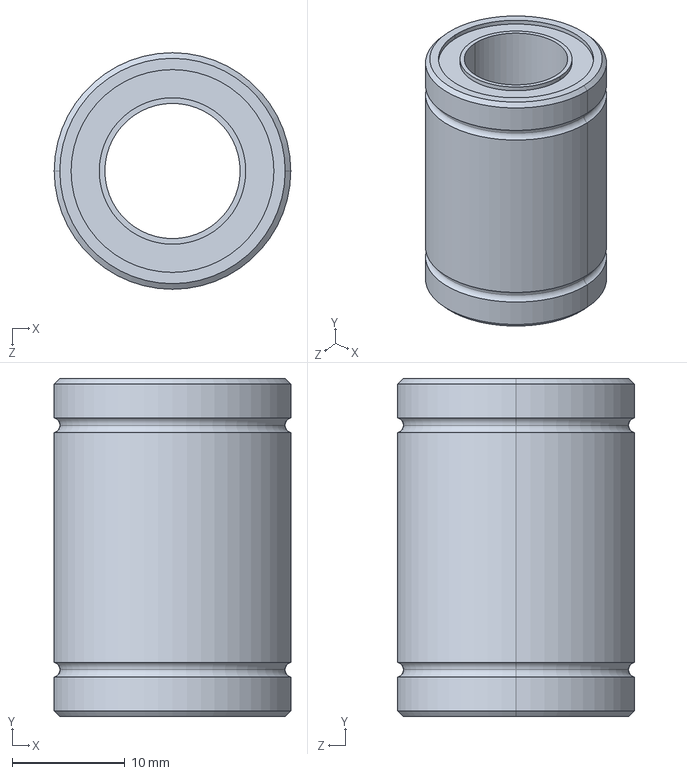
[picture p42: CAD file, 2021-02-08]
CAD/Build 1/Traceparts/LM12UU.STEP
21.0 x 30.0 x 21.0 mm

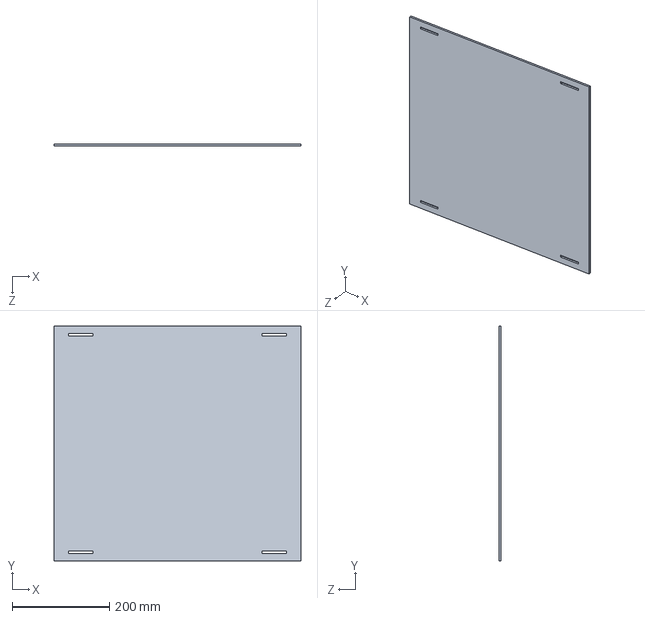
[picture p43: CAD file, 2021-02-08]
CAD/Build 2/base.SLDPRT
508.0 x 482.6 x 5.00 mm

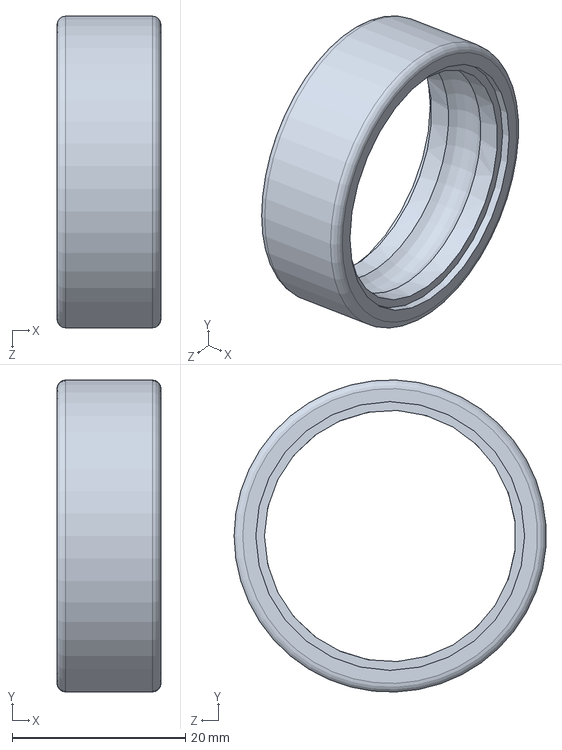
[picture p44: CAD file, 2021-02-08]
CAD/Build 1/Bearing/Outer Race.SLDPRT
12.0 x 36.0 x 36.0 mm

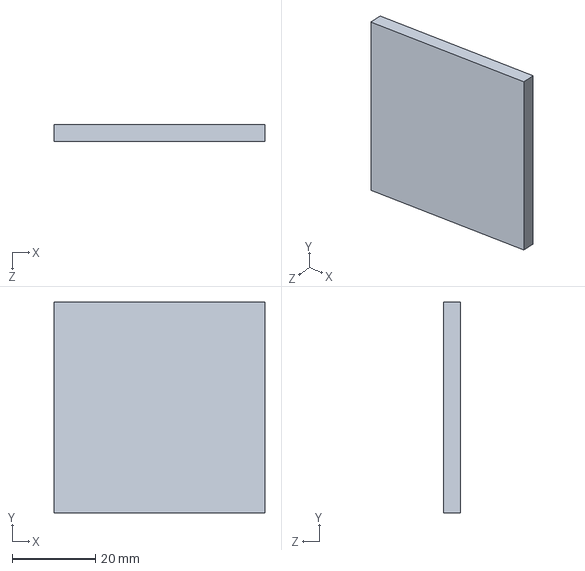
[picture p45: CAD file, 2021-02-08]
CAD/Build 1/board_white.SLDPRT
50.8 x 50.8 x 4.00 mm

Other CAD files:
CAD/Build 2/Pieces/P_Black_Knight.SLDPRT
CAD/Build 1/ChessPieces/King.SLDPRT
CAD/Build 1/Traceparts/support_sk25.SLDPRT
CAD/Build 2/Pieces/P_White_Pawn.SLDPRT
CAD/Build 1/Bearing/Ball.SLDPRT
CAD/Build 1/Bearing/Cage.SLDPRT
CAD/Build 1/Bearing/Inner Race.SLDPRT
CAD/Build 1/Board.SLDPRT
CAD/Build 1/Board2.SLDPRT
CAD/Build 1/ChessPieces/Bishop.SLDPRT
CAD/Build 1/ChessPieces/Pawn.SLDPRT
CAD/Build 1/Grabcad/pillow block 25mm detailed.SLDPRT
CAD/Build 1/MagnetMount.SLDPRT
CAD/Build 1/RailMount.SLDPRT
CAD/Build 1/RailMount2.SLDPRT
CAD/Build 1/Traceparts/LM12UU.IGS
CAD/Build 1/Traceparts/LM12UU.SLDPRT
CAD/Build 1/board_base.SLDPRT
CAD/Build 1/board_dark.SLDPRT
CAD/Build 1/groundPlate.SLDPRT
CAD/Build 1/rail12mm.SLDPRT
CAD/Build 1/rail12mmShort.SLDPRT
CAD/Build 1/stepper.SLDPRT
CAD/Build 2/Board2.SLDPRT
CAD/Build 2/Pieces/P_Black_Bishop.SLDPRT
CAD/Build 2/Pieces/P_Black_King.SLDPRT
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

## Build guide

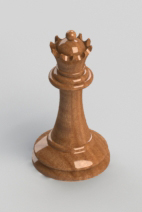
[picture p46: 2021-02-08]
CAD/Build 1/ChessPieces/Renders/Queen Light.JPG

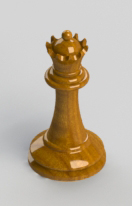
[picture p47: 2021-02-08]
CAD/Build 1/ChessPieces/Renders/Queen Yellow.JPG

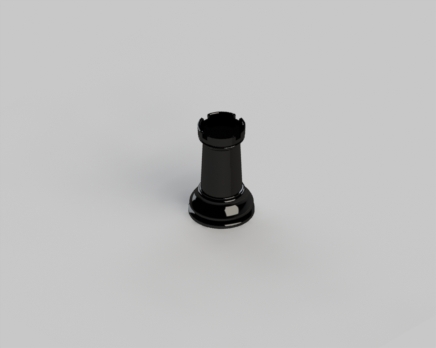
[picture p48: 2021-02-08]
CAD/Build 1/ChessPieces/Renders/Rook Dark.JPG

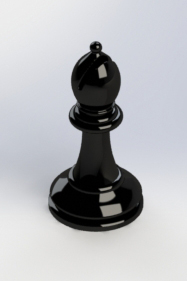
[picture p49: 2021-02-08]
CAD/Build 1/ChessPieces/Renders/Bishop Dark.JPG

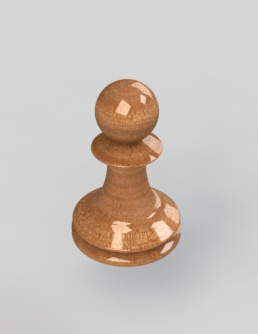
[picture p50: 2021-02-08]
CAD/Build 1/ChessPieces/Renders/Pawn Light.jpg

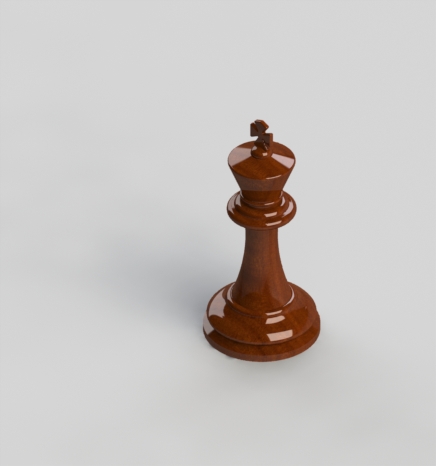
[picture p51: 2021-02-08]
CAD/Build 1/ChessPieces/Renders/King Brown.JPG

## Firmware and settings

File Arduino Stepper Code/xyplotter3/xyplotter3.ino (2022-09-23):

#include <Servo.h>
#define t 3
int X[] = {2, 3, 4, 5};
int Y[] = {6, 7, 8, 9};
Servo Cursor;
void mX(int dir);
void mY(int dir);
void moveXY(int X, int Y);
void textHandle(int X,int Y, int grab);

void setup() {
  Serial.begin(9600);
  pinMode(2, OUTPUT);
  pinMode(3, OUTPUT);
  pinMode(4, OUTPUT);
  pinMode(5, OUTPUT);
  pinMode(6, OUTPUT);
  pinMode(7, OUTPUT);
  pinMode(8, OUTPUT);
  pinMode(9, OUTPUT);
  Cursor.attach(12);
  Cursor.write(30);
}

void loop() {
  char c = 0, xdir, ydir,string[12]={0};
  int n = 0, X = 0, Y = 0, grab = 0;
  while (!Serial.available());
  {
    while (1)
    {
      c = Serial.read();
      if (c == 'q')
        break;
      string[n] = c;
      n++;
      while (!Serial.available());
    }
  }

  if (string[0] == 'x' && string[2] == 'y')
  {
    xdir = string[1];
    ydir = string[3];
    for (int i = 4; i < n; i++)
    {
      X = X*10 + string[i] - '0';
      Y = Y*10 + string[i] - '0';
    }
    if (xdir == '-')
      X = -X;
    if (ydir == '-')
      Y = -Y;
  }
  else if (string[0] == 'x')
  {
    xdir = string[1];
    for (int i = 2; i < n; i++)
    {
      X = X*10 + string[i] - '0';
    }
    if (xdir == '-')
      X = -X;
  }
  else if (string[0] == 'y')
  {
    ydir = string[1];
    for (int i = 2; i < n; i++)
    {
      Y = Y*10 + string[i] - '0';
    }
    if (ydir == '-')
      Y = -Y;
  }
  else if (string[0] == 'g')
    grab = 1;
  else if (string[0] == 'r')
    grab = -1;
  else
    return;

  textHandle(X,Y,grab);
}

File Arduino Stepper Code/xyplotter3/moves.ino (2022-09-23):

void mX(int dir)
{
  static int pin = 0;
  static int state = 0;
  static int prevdir = 0;
  if (dir > 0)
  {
    if (!state)
    {
      if (prevdir < 0)
      {
        digitalWrite(X[pin], state);
        pin = (pin + 1) % 4;
      }
      else digitalWrite(X[(pin + 3) % 4], state);
    }
    else
    {
      pin = (pin + 1) % 4;
      digitalWrite(X[pin], state);
    }
    state = !state;
    prevdir = dir;
  }
  else if (dir < 0)
  {
    if (!state)
    {
      if (prevdir > 0)
      {
        digitalWrite(X[pin], state);
        pin = (pin + 3) % 4;
      }
      else digitalWrite(X[(pin + 1) % 4], state);
    }
    else
    {
      pin = (pin + 3) % 4;
      digitalWrite(X[pin], state);
    }
    state = !state;
    prevdir = dir;
  }
}


void mY(int dir)
{
  static int pin = 0;
  static int state = 0;
  static int prevdir = 0;
  if (dir > 0)
  {
    if (!state)
    {
      if (prevdir < 0)
      {
        digitalWrite(Y[pin], state);
        pin = (pin + 1) % 4;
      }
      else digitalWrite(Y[(pin + 3) % 4], state);
    }
    else
    {
      pin = (pin + 1) % 4;
      digitalWrite(Y[pin], state);
    }
    state = !state;
    prevdir = dir;
  }
  else if (dir < 0)
  {
    if (!state)
    {
      if (prevdir > 0)
      {
        digitalWrite(Y[pin], state);
        pin = (pin + 3) % 4;
      }
      else digitalWrite(Y[(pin + 1) % 4], state);
    }
    else
    {
      pin = (pin + 3) % 4;
      digitalWrite(Y[pin], state);
    }
    state = !state;
    prevdir = dir;
  }
}


void moveXY(int X, int Y)
{
  for (int i = 0; i < 8; i++)
  {
    mX(X);
    mY(Y);
    delay(t);
  }
}
